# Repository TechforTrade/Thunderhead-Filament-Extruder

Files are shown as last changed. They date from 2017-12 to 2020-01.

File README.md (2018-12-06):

# Thunderhead Filament Extruder

The Thunderhead filament extruder is a  small scale extruder designed by Techfortrade that can be used for recycling PET plastic bottle flake directly into 3D printing filament. A special emphasis throughout the design has been placed on using affordable and easily attainable materials. This repository serves as a host for the documentation and code used with the machine. We are using GrabCAD Workbench for the hardware development and will place snapshots of the CAD files here on Github with each release. Current (though not necessarily stable) files can be accessed on our [GrabCAD partner space](https://workbench.grabcad.com/workbench/projects/gcvN9Xsi01SW-lFGhJRj_-4vqndCMFAaoUt_-UQBdidnVn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).

#### The Thunderhead converts clean and dry PET flake into 3D printing Filament
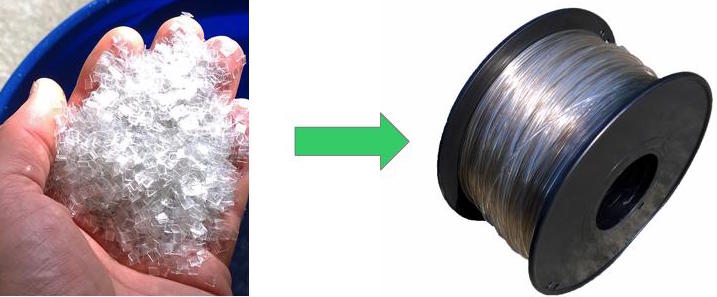
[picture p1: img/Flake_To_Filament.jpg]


# Table of Contents

- [Goals](#goals)
- [PET Plastic](#pet-plastic)
- [Safety and Liability](#safety-and-liability)
- [Building the Thunderhead](#building-the-thunderhead)
- [Software](#software)
- [Operation](#operation)
- [Contributing](#contributing)
- [Maintainers](#maintainers)
- [Acknowledgements](#acknowledgements)
- [License](#license)

## Goals
The Thunderhead is designed with the intent of making it possible to recycle plastic from the post consumer waste stream into 3D printing filament on a small scale with minimal start up capital required. This makes the following possible:
- Low cost 3D printing filament anywhere in the world
- Enable local capture of the value contained in waste plastic
- Access to expensive or hard to find items via 3D printing (eg. [Open Flexure Microscope](https://github.com/rwb27/openflexure_microscope))
- Small scale business opportunities without need for large amounts of capital
- Enable local recycling where it is otherwise not possible

## PET Plastic 
The Thunderhead is designed to extrude Polyethylene Terephthalate (PET or PETE) for the following reasons:

-  Prints  very well on printers such as the Retr3D
-  Easy to find nearly anywhere on the planet
-  Has good physical properties
-  Reasonably safe to work with, especially compared to ABS which often has Brominated Flame Retardants (BFR)

PET is easily identified by the following symbol usually located on the bottom on the bottle:

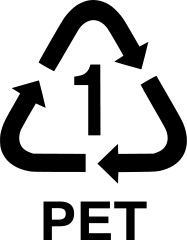
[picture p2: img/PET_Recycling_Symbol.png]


There are some challenges to working with PET plastic. A few these are described below. Follow the links to get more detailed information on these and other challenges:

* **Crystalization** - PET crystalizes when cooled slowly. To avoid making filament that is brittle like glass, a water bath is used.
* **Low Viscosity** - When PET melts it has a low viscosity and a low melt strength which makes it difficult to pull into a filament with an even diameter. The Thunderhead uses a cooling tube to help increase the viscosity and melt strength before the plastic leaves the extruder. The water bath also helps to 
* **Hygroscopicity** - PET pulls water out of the air and holds on to it. This water can cause problems during extrusion and printing such as air bubbles, foaming and degredation of the plastic.
* **Hydrolysis** - The polymer chains in PET can break down in the presence of water at elevated temperatures. When this happens, the viscosity of the melt is reduced, making it difficult to extrude. To Avoid this problem, the plastic flakes must be thoroughly dried just before extrusion. 

## Safety and Liability

You are responsible for your own safety. This machine is under development. Please see the text in the license regarding **Disclaimer of Warranties and Limitation of Liability**.

## Building the Thunderhead

Please refer to our [wiki](https://github.com/TechforTrade/Thunderhead-Filament-Extruder/wiki) for detailed information on building the Thunderhead. 

#### Major Tools Needed ####

Note that you don't necessarily have to own all of these tools. A local shop could do some of the work for you. Especially the lathe and milling work. See the Wiki for a more exhaustive list.

* Drill Press
* Metal Lathe - Threading the barrel and making the shaft for the gear box
* Welding (stick, oxy-acetalene, etc.) - For welding frames together
* 3D printer - Many of the complex parts in the machine are 3D printed
* Milling Machine (optional) - For milling flats into a few parts. Could be done with grinder and hand files though more time consuming.
* Horizontal band saw (optional) - For cutting stock metal to size. A hacksaw and vice will work, but will be slower.

#### Major Components of the Thunderhead

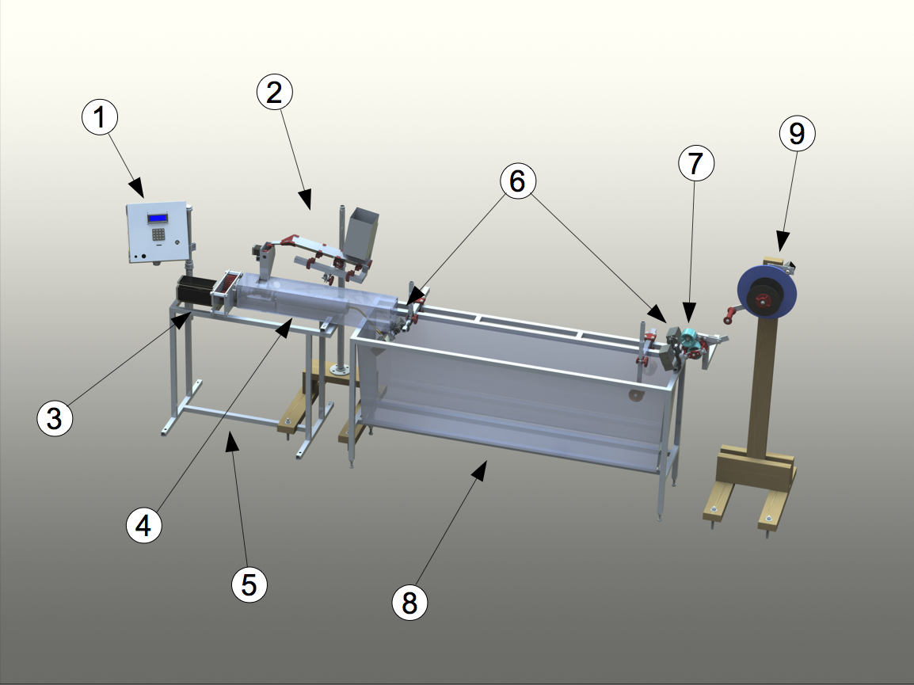
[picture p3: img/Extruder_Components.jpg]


1. **Control Box** - Contains the power supply, Arduino, and other circuitry needed to operate the extruder. Note: The starve feeder, diameter sensors and spooler have their own control circuitry and communicate with the master Arduino via IIC.
2. **Starve Feeder**- Used to add flakes to the extruder at a constent rate. Subcomponents are:
   1. Hopper - Holdes flake ready to be extruded
   2. Vibratory Conveyer - Moves flake to the balance and keeps flake from bridging, and rat holing.
   3. Balance - Weighs out small portions of flake and then delivers them to the extruder at a constant rate. Feedback from the balance controls the vibratory conveyer.
3. **Auger Motor and Gear Box** - A large NEMA 42 stepper motor and 3:1 gear box with 3D printed gears. The stepper alows for speed control and the gearbox increases the torque on the auger.
4. **Extruder Body** - The extruder body has many components. The main components are:
   1. Feed Throat - Location where the plastic enters the barrel. Made with internal grooves to improve the feeding of the plastic into the barrel.
   2. Auger - A 1/2 in. diameter, 18 in. long wood auger used to convey the plastic through the barrel. NOTE: This is not designed for plastics extrusion and performs significantly worse than a plastic extrusion screw would. It is much less expensive though.
   3. Barrel - 1/2in I.D. DOM metal pipe through which the auger pushes the plastic. It has two heating zones that are heated by 104 watt 1/2 in. fiberglass insulated heating tape.
   4. Breaker plate - A small disk of metal with a number of holes drilled into it at the downstream end of the barrel. It acts to reduce the twist in the plastic that is caused by the screw, reducing what is called "screw beat" and improving the uniformity of the diameter. 
   5. Cooling tube - A brass tube at the end of the barrel that reduces the temperature of the plastic melt in order to increase its viscosity. The bend in the tube helps to aim the filament at the guide roller at the end of the water bath and improve roundness of the filament. It has two heating zones.
   6. Nozzle - determines diameter of melt as it leaves the extruder. Equiped with its own heating zone so that surface quality of the filament can be improved.
5. **Extruder Stand** - Supports the extruder and has a sheet metal enclosure to collect fumes given off by the extruder.
6. **Diameter Sensors** - Non contact laser diameter sensors with their own control electronics. The first is used to determine the diameter of the melt as it leaves the extruder and control the speed of the outfeed rollers in order to maintain a constant diameter. The second is used to monitor the final diameter and ensure that the set point of the first diameter sensor is correct.
7. **Outfeed Rollers** - Used to pull the filament through the water bath. Their speed determines the diameter of the filament. The rollers are controlled by the primary diameter sensor.
8. **Water Bath** - Used to cool the melt quickly. This is important because otherwise, the PET would neck down to a very small diameter or cool too slowly and crystalize. Crystalized plastic is too brittle to work with a 3D printer.
9. **Spooler** - Winds the filament up onto a spool. The spooler is still being worked on, early designs fought with the outfeed rollers and caused uneven filament diameters.

## Software

Please refer to our [wiki](https://github.com/TechforTrade/Thunderhead-Filament-Extruder/wiki) for detailed information on the use of the various bits of code kept in this repository.

Five firmware installations must be completed to get the Thunderhead up and running. These are:

- **Thunderware.ino** - for the Arduino mega 2560 that controls the machine (located in the controller box)
- **StarveFeeder.ino** - Upload to the Arduino Nano that controls the starve feeder.
- **Diameter_Sensor.ino (x2)** - Install on <u>both</u> the primary and QC diameter sensor Arduino Nanos.
- **Spooler.ino** - Upload to the Arduino Nano that controls the spooler.

Additionally, there is code written in Processing called **Extruder_Data_visualizer.pde** that produces real time graphs of the the output of the diameter sensors as well as the outfeed roller RPM. This can be useful for tuning the PID in the primary diameter sensor that controls the filament diameter.

## Operation

Detailed operation instructions with tips and trouble shooting are located in our [wiki](https://github.com/TechforTrade/Thunderhead-Filament-Extruder/wiki). The following summarizes basic operation. Video of this process can be found here.

#### Preparation

Before extruding, the clean PET flake must be dried. This must happen just before extruding because the PET will absorb water out of the air at room temperature. Dry the PET in a bench top oven (toaster oven) at a temperature between 150 and 170 °C for four hours. Do this in a well ventilated area. It is recomended to capture and vent the fumes with a fume hood and duct. Do not exceed 175 °C as the plastic will begin to degrade. Keep the flake in the oven until the extruder is ready to begin extruding so that the flake is exposed to room temperature air for as little time as possible.

#### Extruding

Steps

1. Power up the extruder. 
2. Select the menu option "Select Profile". For this and all following steps:
   1.  'A' is used to scroll up.
   2.  'B' is used to scoll down.
   3.  'C' is used to select.
3. Select the profile you want.
4. Select "Extrude".
   1. The extruder will enter the Preheat state, and warm the heating zones to the initial set temps.
5. When the initial set temps have been reached, the extruder will automatically enter the Soak state and soak for the number of minutes specified in the profile.
6. While the extruder is in the Soak state do the following:
   1. Remove the plastic from the oven and add it to the hopper.
   2. Home the balance by rotating the balance counter clockwise as far as it will go and then selecting "Home Balance" from the menu.
   3. Select "Feed Plastic" to turn the vibratory conveyer on.
   4. Turn the vibratory conveyor off when the flake has moved to then end of the conveyor and is about to begin filling the bucket by selecting "Feed Plastic" again.
7. At the end of the Soak state (default time is 8 minutes) the extruder will automatically enter the Extrude state.
8. Turn on the starve feeder by selecting "Starve Feeder".
9. When plastic begins to flow out of the nozzle, use the start up tool to guide the filament under the guide roller in the water bath and then place the filament between the outfeed rollers.
10. Reduce the temperatures to the extruding temperatures (the cooling tube and nozzle temps are lowered) by selecting  "Set Extrude Temps" from the menu.
11. Increase the diameter of the filament to the desired diameter by reducing the outfeed RPM. Do this by selecting "Outfeed RPM" and entering the desired rpm (typically around 18).
12. Clip off the initial section of filament that is not of the correct diameter.
13. Load the filament into the spooler and turn it on. 
14. If desired, automatic control of the outfeed roller rpm can be engaged by selecting "OF Mode". It will change from "man" to "auto". The rpm of the outfeed rollers will now be automatically adjusted to maintain the "Dia Setpoint".

#### Stopping the Extruder

At any point during the extrusion (including preheat and soak) the extruder can be stopped by pressing 'D'. You will be asked to confirm by pressing 'A' or cancel by pressing 'B'. The machine can also simply be powered off.

## Contributing

We'd love your help! You can contribute in many ways. Here are a few:

* Technical support on designs, code etc.
* Help improve the wiki and other documentation.
* Testing. Different Extrusion parameters, code, etc.
* Connect us with other interested individuals and groups.
* Donate! [Techfortrade](http://www.techfortrade.org/) is a non profit organization working to create business opportunities in low resource settings.
<a href="https://www.globalgiving.org/projects/digital-blacksmiths-3d-printing-from-trash/">Donate Now</a>

## On Going Work

All the of the most up to date CAD files can be found [here on our GrabCAD Workbench](https://workbench.grabcad.com/workbench/projects/gcvN9Xsi01SW-lFGhJRj_-4vqndCMFAaoUt_-UQBdidnVn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). The following are a few ideas that we are hoping to pursue:

### Planned Improvements and Experiments ###

#### Feedback Control####

The non-contact diameter sensors are now working so we can get real time information on diameter. The code for using feedback control to maintain constant diameter is also mostly in place. What needs to be done now is to find the correct  placement of the sensor and tune the PID. 

#### Drying hopper ####

Currently the plastic is dried and then put into the hopper where it sits and
absorbs moisture. With a drying hopper, the plastic would be continuously dried
and would have no chance to absorb moisture before entering the machine. This
may help improve the melt viscosity and consistency by reducing the amount of polymer
hydrolysis.

#### New Filament Support/Guiding Strategy ####
The shape and diameter of the filament is essentially set when the hot plastic
enters the water bath. Unwanted movement of the filament down stream from this
point can greatly impact the shape of the filament. New strategies for guiding
the filament in a controlled manner need to be explored. 

#### Nozzle Geometry and Drawdown ####
It may be fruitful to explore different nozzle geometries and the amount and
rate of drawdown. What are the optimal conditions for consistent filament?

#### Test Different Sources of PET ####
Not all PET resins are the same. By testing resins from various bottle sources
and even virgin pellets, it may be possible to determine whether or not some
sources have more desirable characteristics than others.

#### Melt Filter ####
A screen should be added just up stream of the breaker plate. This screen will
catch debris and improve the quality of the filament. A down side is that a melt filter may reduce, perhaps greatly, the output of the machine.

#### Explore potential additives

Desiccating agents such as CaO (quicklime) or even Portland cement might
possibly be added to scavenge water remaining in the melt, which would help
improve viscosity. Nucleating agents such as sodium benzoate and talc might be
used to encourage crystal growth, growing more numerous and smaller crystals
which may help to reduce the brittleness of crystalline polymer. Could this be a route to producing printable crystalline PET?

## Maintainers

[Matthew Rogge](https://github.com/Maaphoo) and [Michael Uttmark](https://github.com/biosafetylvl5) are currently the maintainers of this
repository.

## Acknowledgements

The following people and organizations provided valuable help and guidance over
the course of the project:

**Matt Clark** who provided hundreds of free man hours to assist with the re-design process.

**Frank Schoofs** who volunteered his material science expertise to assist with thermal modeling required to design heating and cooling sections of the extruder.

**Vasileios Grammatikakis** an electronics expert who has assisted with improvements to the Thunderhead electronics.

**Unilever plc.** whose PET specialists have provided insights into working with PET, drying, and testing.

## 

## License


This work is licensed under a <a rel="license" href="http://creativecommons.org/licenses/by-sa/4.0/">Creative Commons Attribution-ShareAlike 4.0 International License</a>.

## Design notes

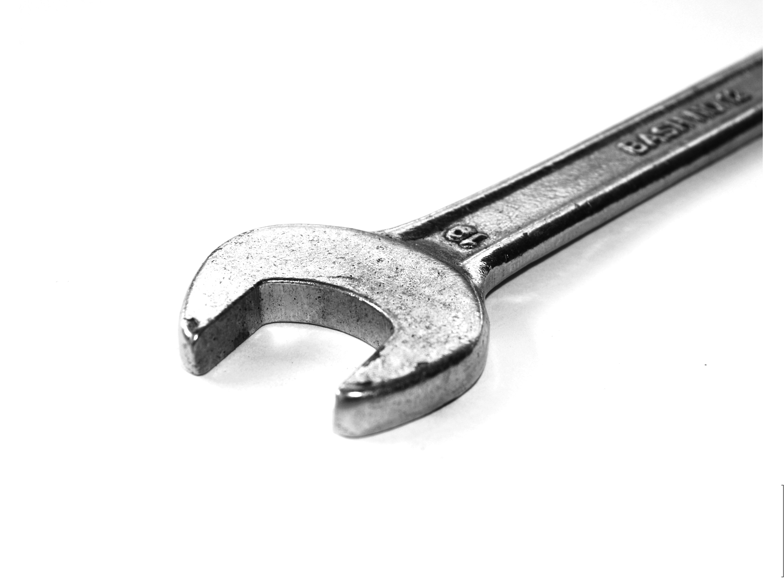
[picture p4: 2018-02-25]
img/Tools/wrench.jpg

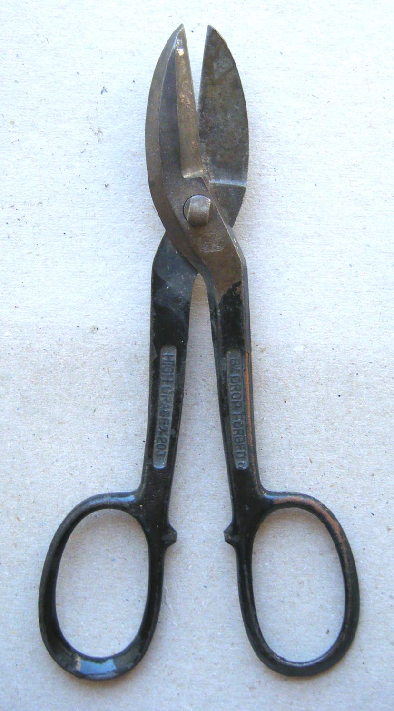
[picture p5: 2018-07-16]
img/Tools/Tin Snips.jpg

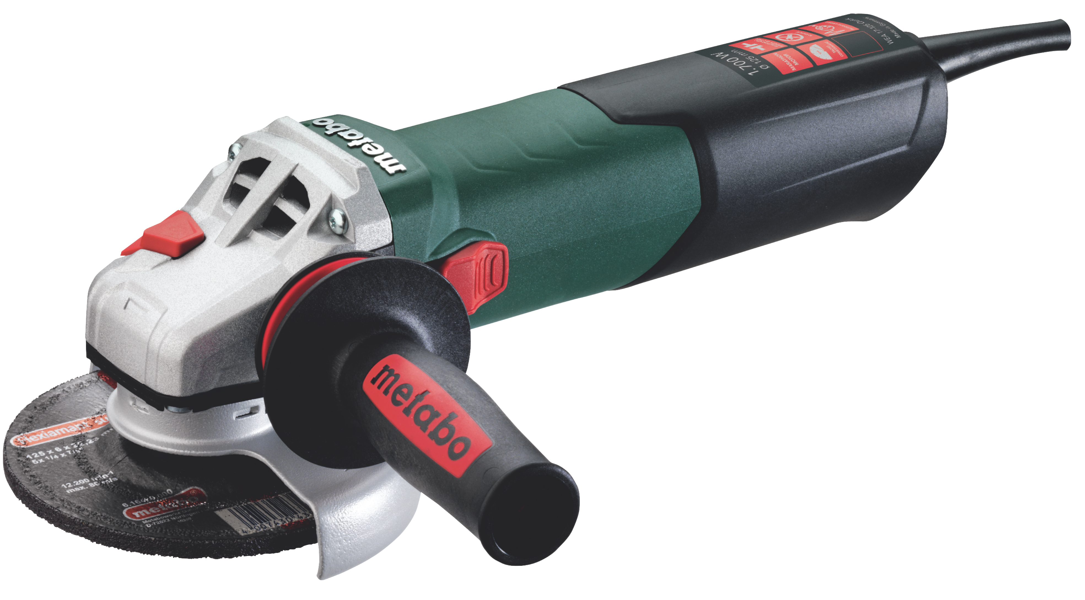
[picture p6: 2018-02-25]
img/Tools/Angle Grinder.jpg

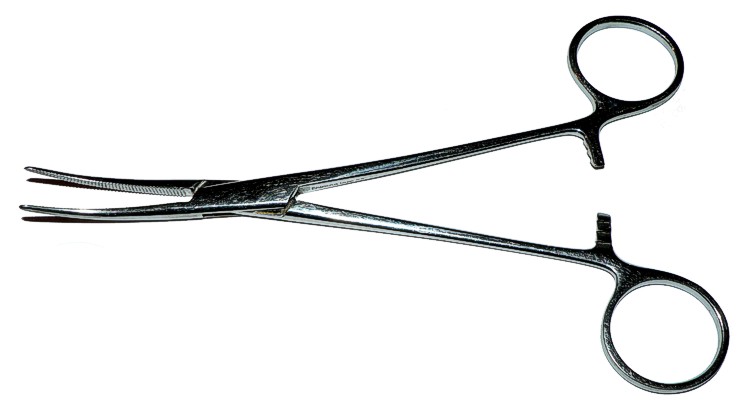
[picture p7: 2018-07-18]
img/Tools/Hemostat.jpg

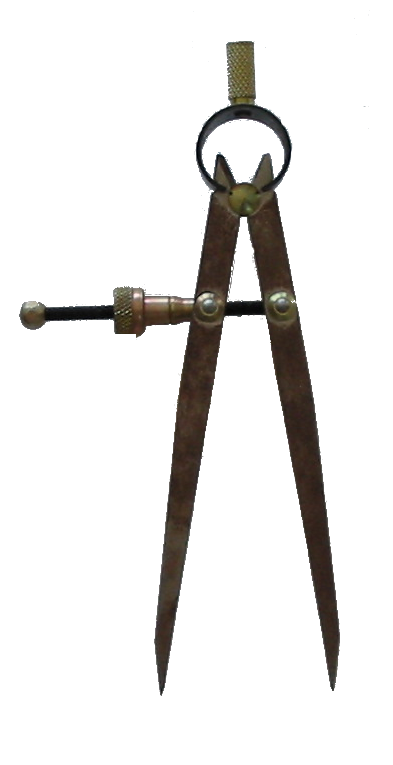
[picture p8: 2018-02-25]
img/Tools/Spring Divider.png

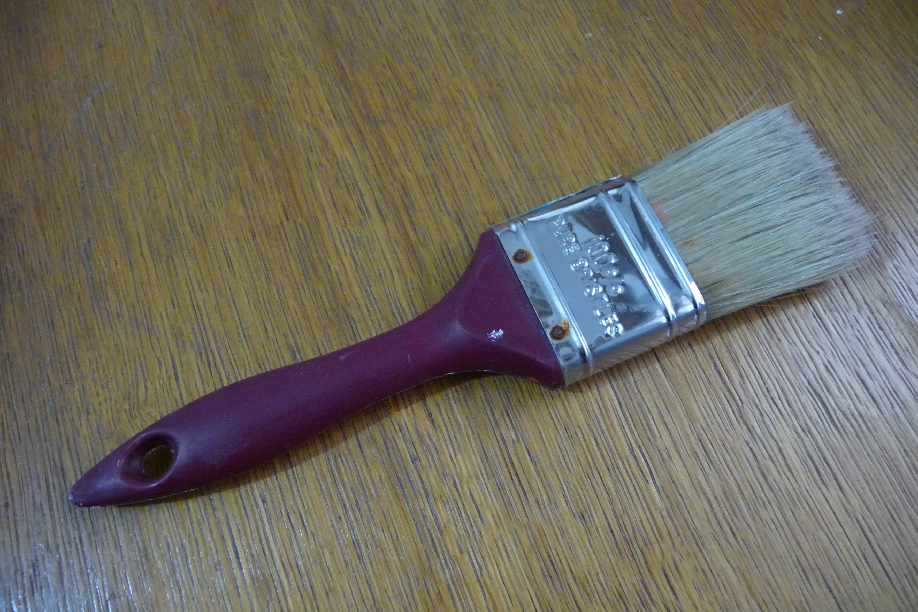
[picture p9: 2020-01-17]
img/Tools/Paint Brush.jpg

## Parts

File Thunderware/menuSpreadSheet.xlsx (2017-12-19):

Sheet: Sheet1
id | Text | parent | child | value | precision | type | action
0 | root | -1 | 1 | NULL | 0 | Menu::TITLE | NULL | {rootStr, -1, 1, NULL, 0, Menu::TITLE, NULL},
1 | selectProfile | 0 | 4 | NULL | 0 | Menu::TITLE | NULL | {selectProfileStr, 0, 4, NULL, 0, Menu::TITLE, NULL},
2 | calibrate | 0 | 35 | NULL | 0 | Menu::TITLE | NULL | {calibrateStr, 0, 35, NULL, 0, Menu::TITLE, NULL},
3 | auxiliary | 0 | 119 | NULL | 0 | Menu::TITLE | NULL | {auxiliaryStr, 0, 119, NULL, 0, Menu::TITLE, NULL},
4 | profile0 | 1 | 15 | &configuration.profileNames[0] | 0 | Menu::TITLE_STRING | &loadProfile0 | {profile0Str, 1, 15, &configuration.profileNames[0], 0, Menu::TITLE_STRING, &loadProfile0},
5 | profile1 | 1 | 15 | &configuration.profileNames[1] | 0 | Menu::TITLE_STRING | &loadProfile1 | {profile1Str, 1, 15, &configuration.profileNames[1], 0, Menu::TITLE_STRING, &loadProfile1},
6 | profile2 | 1 | 15 | &configuration.profileNames[2] | 0 | Menu::TITLE_STRING | &loadProfile2 | {profile2Str, 1, 15, &configuration.profileNames[2], 0, Menu::TITLE_STRING, &loadProfile2},
7 | profile3 | 1 | 15 | &configuration.profileNames[3] | 0 | Menu::TITLE_STRING | &loadProfile3 | {profile3Str, 1, 15, &configuration.profileNames[3], 0, Menu::TITLE_STRING, &loadProfile3},
8 | profile4 | 1 | 15 | &configuration.profileNames[4] | 0 | Menu::TITLE_STRING | &loadProfile4 | {profile4Str, 1, 15, &configuration.profileNames[4], 0, Menu::TITLE_STRING, &loadProfile4},
9 | profile5 | 1 | 15 | &configuration.profileNames[5] | 0 | Menu::TITLE_STRING | &loadProfile5 | {profile5Str, 1, 15, &configuration.profileNames[5], 0, Menu::TITLE_STRING, &loadProfile5},
10 | profile6 | 1 | 15 | &configuration.profileNames[6] | 0 | Menu::TITLE_STRING | &loadProfile6 | {profile6Str, 1, 15, &configuration.profileNames[6], 0, Menu::TITLE_STRING, &loadProfile6},
11 | profile7 | 1 | 15 | &configuration.profileNames[7] | 0 | Menu::TITLE_STRING | &loadProfile7 | {profile7Str, 1, 15, &configuration.profileNames[7], 0, Menu::TITLE_STRING, &loadProfile7},
12 | profile8 | 1 | 15 | &configuration.profileNames[8] | 0 | Menu::TITLE_STRING | &loadProfile8 | {profile8Str, 1, 15, &configuration.profileNames[8], 0, Menu::TITLE_STRING, &loadProfile8},
13 | profile9 | 1 | 15 | &configuration.profileNames[9] | 0 | Menu::TITLE_STRING | &loadProfile9 | {profile9Str, 1, 15, &configuration.profileNames[9], 0, Menu::TITLE_STRING, &loadProfile9},
14 | defaultProfile | 1 | 15 | NULL | 0 | Menu::TITLE | &loadDefaultProfile | {defaultProfileStr, 1, 15, NULL, 0, Menu::TITLE, &loadDefaultProfile},
15 | extrude | 4 | -1 | NULL | 0 | Menu::TITLE | &actionExtrude | {extrudeStr, 4, -1, NULL, 0, Menu::TITLE, &actionExtrude},
16 | saveProfile | 4 | -1 | NULL | 0 | Menu::TITLE | &saveCurrentProfile | {saveProfileStr, 4, -1, NULL, 0, Menu::TITLE, &saveCurrentProfile},
17 | profileName | 4 | -1 | &configuration.profile.name | 0 | Menu::STRING | NULL | {profileNameStr, 4, -1, &configuration.profile.name, 0, Menu::STRING, NULL},
18 | diaSetpoint | 4 | -1 | &configuration.profile.diaSetpoint | 2 | Menu::DOUBLE | NULL | {diaSetpointStr, 4, -1, &configuration.profile.diaSetpoint, 2, Menu::DOUBLE, NULL},
19 | density | 4 | -1 | &configuration.profile.density | 2 | Menu::DOUBLE | NULL | {densityStr, 4, -1, &configuration.profile.density, 2, Menu::DOUBLE, NULL},
20 | tolerance | 4 | -1 | &configuration.profile.tolerance | 2 | Menu::FLOAT | NULL | {toleranceStr, 4, -1, &configuration.profile.tolerance, 2, Menu::FLOAT, NULL},
21 | gramsPerMin | 4 | -1 | &configuration.profile.gramsPerMin | 2 | Menu::FLOAT | NULL | {gramsPerMinStr, 4, -1, &configuration.profile.gramsPerMin, 2, Menu::FLOAT, NULL},
22 | augerRPM | 4 | -1 | &configuration.profile.augerRPM | 1 | Menu::FLOAT | NULL | {augerRPMStr, 4, -1, &configuration.profile.augerRPM, 1, Menu::FLOAT, NULL},
23 | outfeedRPM | 4 | -1 | &configuration.profile.outfeedRPM | 1 | Menu::DOUBLE | NULL | {outfeedRPMStr, 4, -1, &configuration.profile.outfeedRPM, 1, Menu::DOUBLE, NULL},
24 | soakTime | 4 | -1 | &configuration.profile.soakTime | 0 | Menu::DOUBLE | NULL | {soakTimeStr, 4, -1, &configuration.profile.soakTime, 0, Menu::DOUBLE, NULL},
25 | zone1InitialSetTemp | 4 | -1 | &configuration.profile.zone1InitialSetTemp | 0 | Menu::DOUBLE | NULL | {zone1InitialSetTempStr, 4, -1, &configuration.profile.zone1InitialSetTemp, 0, Menu::DOUBLE, NULL},
26 | zone2InitialSetTemp | 4 | -1 | &configuration.profile.zone2InitialSetTemp | 0 | Menu::DOUBLE | NULL | {zone2InitialSetTempStr, 4, -1, &configuration.profile.zone2InitialSetTemp, 0, Menu::DOUBLE, NULL},
27 | zone3InitialSetTemp | 4 | -1 | &configuration.profile.zone3InitialSetTemp | 0 | Menu::DOUBLE | NULL | {zone3InitialSetTempStr, 4, -1, &configuration.profile.zone3InitialSetTemp, 0, Menu::DOUBLE, NULL},
28 | zone4InitialSetTemp | 4 | -1 | &configuration.profile.zone4InitialSetTemp | 0 | Menu::DOUBLE | NULL | {zone4InitialSetTempStr, 4, -1, &configuration.profile.zone4InitialSetTemp, 0, Menu::DOUBLE, NULL},
29 | zone5InitialSetTemp | 4 | -1 | &configuration.profile.zone5InitialSetTemp | 0 | Menu::DOUBLE | NULL | {zone5InitialSetTempStr, 4, -1, &configuration.profile.zone5InitialSetTemp, 0, Menu::DOUBLE, NULL},
30 | zone1SetTemp | 4 | -1 | &configuration.profile.zone1SetTemp | 0 | Menu::DOUBLE | NULL | {zone1SetTempStr, 4, -1, &configuration.profile.zone1SetTemp, 0, Menu::DOUBLE, NULL},
31 | zone2SetTemp | 4 | -1 | &configuration.profile.zone2SetTemp | 0 | Menu::DOUBLE | NULL | {zone2SetTempStr, 4, -1, &configuration.profile.zone2SetTemp, 0, Menu::DOUBLE, NULL},
32 | zone3SetTemp | 4 | -1 | &configuration.profile.zone3SetTemp | 0 | Menu::DOUBLE | NULL | {zone3SetTempStr, 4, -1, &configuration.profile.zone3SetTemp, 0, Menu::DOUBLE, NULL},
33 | zone4SetTemp | 4 | -1 | &configuration.profile.zone4SetTemp | 0 | Menu::DOUBLE | NULL | {zone4SetTempStr, 4, -1, &configuration.profile.zone4SetTemp, 0, Menu::DOUBLE, NULL},
34 | zone5SetTemp | 4 | -1 | &configuration.profile.zone5SetTemp | 0 | Menu::DOUBLE | NULL | {zone5SetTempStr, 4, -1, &configuration.profile.zone5SetTemp, 0, Menu::DOUBLE, NULL},
35 | saveConfig | 2 | -1 | NULL | 0 | Menu::ACTION | &saveConfig | {saveConfigStr, 2, -1, NULL, 0, Menu::ACTION, &saveConfig},
36 | starveFeederConfig | 2 | 41 | NULL | 0 | Menu::TITLE | NULL | {starveFeederConfigStr, 2, 41, NULL, 0, Menu::TITLE, NULL},
37 | augerConfig | 2 | 65 | NULL | 0 | Menu::TITLE | NULL | {augerConfigStr, 2, 65, NULL, 0, Menu::TITLE, NULL},
38 | heaterConfig | 2 | 71 | NULL | 0 | Menu::TITLE | NULL | {heaterConfigStr, 2, 71, NULL, 0, Menu::TITLE, NULL},
39 | outfeedConfig | 2 | 109 | NULL | 0 | Menu::TITLE | NULL | {outfeedConfigStr, 2, 109, NULL, 0, Menu::TITLE, NULL},
40 | spoolerConfig | 2 | 110 | NULL | 0 | Menu::TITLE | NULL | {spoolerConfigStr, 2, 110, NULL, 0, Menu::TITLE, NULL},
41 | homeStarveFeeder | 36 | -1 | NULL | 0 | Menu::ACTION | &homeStarveFeeder | {homeStarveFeederStr, 36, -1, NULL, 0, Menu::ACTION, &homeStarveFeeder},
42 | dump | 36 | -1 | NULL | 0 | Menu::ACTION | &dump | {dumpStr, 36, -1, NULL, 0, Menu::ACTION, &dump},
43 | feed | 36 | -1 | &feedMode | 0 | Menu::STRING_LOCKED | &feed | {feedStr, 36, -1, &feedMode, 0, Menu::STRING_LOCKED, &feed},
44 | sendCycles | 36 | -1 | NULL | 0 | Menu::ACTION | &sendCyclesToStarveFeeder | {sendCyclesStr, 36, -1, NULL, 0, Menu::ACTION, &sendCyclesToStarveFeeder},
45 | cyclesToSendToStarveFeeder | 36 | -1 | &cyclesToSendToStarveFeeder | 0 | Menu::INT | NULL | {cyclesToSendToStarveFeederStr, 36, -1, &cyclesToSendToStarveFeeder, 0, Menu::INT, NULL},
46 | sendTime | 36 | -1 | NULL | 0 | Menu::ACTION | &sendTimeToStarveFeeder | {sendTimeStr, 36, -1, NULL, 0, Menu::ACTION, &sendTimeToStarveFeeder},
47 | timeToSendToStarveFeeder | 36 | -1 | &timeToSendToStarveFeeder | 0 | Menu::INT | NULL | {timeToSendToStarveFeederStr, 36, -1, &timeToSendToStarveFeeder, 0, Menu::INT, NULL},
48 | gramsPerMin | 36 | -1 | &configuration.profile.gramsPerMin | 2 | Menu::FLOAT | NULL | {gramsPerMinStr, 36, -1, &configuration.profile.gramsPerMin, 2, Menu::FLOAT, NULL},
49 | stop | 36 | -1 | NULL | 0 | Menu::ACTION | &stopStarveFeeder | {stopStr, 36, -1, NULL, 0, Menu::ACTION, &stopStarveFeeder},
50 | starveFeederSlaveAddress | 36 | -1 | &configuration.physical.starveFeederSlaveAddress | 0 | Menu::INT | NULL | {starveFeederSlaveAddressStr, 36, -1, &configuration.physical.starveFeederSlaveAddress, 0, Menu::INT, NULL},
51 | starveFeederLumpMass | 36 | -1 | &configuration.physical.starveFeederLumpMass | 2 | Menu::FLOAT | NULL | {starveFeederLumpMassStr, 36, -1, &configuration.physical.starveFeederLumpMass, 2, Menu::FLOAT, NULL},
52 | starveFeederHomePosition | 36 | -1 | &configuration.physical.starveFeederHomePosition | 0 | Menu::INT | NULL | {starveFeederHomePositionStr, 36, -1, &configuration.physical.starveFeederHomePosition, 0, Menu::INT, NULL},
53 | starveFeederDumpPosition | 36 | -1 | &configuration.physical.starveFeederDumpPosition | 0 | Menu::INT | NULL | {starveFeederDumpPositionStr, 36, -1, &configuration.physical.starveFeederDumpPosition, 0, Menu::INT, NULL},
54 | starveFeederStepDelay | 36 | -1 | &configuration.physical.starveFeederStepDelay | 0 | Menu::INT | NULL | {starveFeederStepDelayStr, 36, -1, &configuration.physical.starveFeederStepDelay, 0, Menu::INT, NULL},
55 | starveFeederHomingStepDelay | 36 | -1 | &configuration.physical.starveFeederHomingStepDelay | 0 | Menu::INT | NULL | {starveFeederHomingStepDelayStr, 36, -1, &configuration.physical.starveFeederHomingStepDelay, 0, Menu::INT, NULL},
56 | starveFeederOverRotation | 36 | -1 | &configuration.physical.starveFeederOverRotation | 0 | Menu::INT | NULL | {starveFeederOverRotationStr, 36, -1, &configuration.physical.starveFeederOverRotation, 0, Menu::INT, NULL},
57 | starveFeederDirection | 36 | -1 | &configuration.physical.starveFeederDirection | 0 | Menu::BOOLEAN | NULL | {starveFeederDirectionStr, 36, -1, &configuration.physical.starveFeederDirection, 0, Menu::BOOLEAN, NULL},
58 | starveFeederVibDutyCycle | 36 | -1 | &configuration.physical.starveFeederVibDutyCycle | 0 | Menu::INT | NULL | {starveFeederVibDutyCycleStr, 36, -1, &configuration.physical.starveFeederVibDutyCycle, 0, Menu::INT, NULL},
59 | starveFeederStartupDutyCycle | 36 | -1 | &configuration.physical.starveFeederStartupDutyCycle | 0 | Menu::INT | NULL | {starveFeederStartupDutyCycleStr, 36, -1, &configuration.physical.starveFeederStartupDutyCycle, 0, Menu::INT, NULL},
60 | starveFeederMaxDutyCycle | 36 | -1 | &configuration.physical.starveFeederMaxDutyCycle | 0 | Menu::INT | NULL | {starveFeederMaxDutyCycleStr, 36, -1, &configuration.physical.starveFeederMaxDutyCycle, 0, Menu::INT, NULL},
61 | starveFeederMinFillTime | 36 | -1 | &configuration.physical.starveFeederMinFillTime | 0 | Menu::INT | NULL | {starveFeederMinFillTimeStr, 36, -1, &configuration.physical.starveFeederMinFillTime, 0, Menu::INT, NULL},
62 | starveFeederMaxFillTime | 36 | -1 | &configuration.physical.starveFeederMaxFillTime | 0 | Menu::INT | NULL | {starveFeederMaxFillTimeStr, 36, -1, &configuration.physical.starveFeederMaxFillTime, 0, Menu::INT, NULL},
63 | starveFeederStartupTime | 36 | -1 | &configuration.physical.starveFeederStartupTime | 0 | Menu::INT | NULL | {starveFeederStartupTimeStr, 36, -1, &configuration.physical.starveFeederStartupTime, 0, Menu::INT, NULL},
64 | starveFeederDebounceTime | 36 | -1 | &configuration.physical.starveFeederDebounceTime | 0 | Menu::INT | NULL | {starveFeederDebounceTimeStr, 36, -1, &configuration.physical.starveFeederDebounceTime, 0, Menu::INT, NULL},
65 | testAuger | 37 | -1 | NULL | 0 | Menu::ACTION | &testAuger | {testAugerStr, 37, -1, NULL, 0, Menu::ACTION, &testAuger},
66 | augerPinSet | 37 | -1 | &configuration.physical.augerPinSet | 0 | Menu::INT | NULL | {augerPinSetStr, 37, -1, &configuration.physical.augerPinSet, 0, Menu::INT, NULL},
67 | augerStepMode | 37 | -1 | &configuration.physical.augerStepMode | 0 | Menu::INT | NULL | {augerStepModeStr, 37, -1, &configuration.physical.augerStepMode, 0, Menu::INT, NULL},
68 | augerDirection | 37 | -1 | &configuration.physical.augerDirection | 0 | Menu::BOOLEAN | NULL | {augerDirectionStr, 37, -1, &configuration.physical.augerDirection, 0, Menu::BOOLEAN, NULL},
69 | augerEnable | 37 | -1 | &configuration.physical.augerEnable | 0 | Menu::BOOLEAN | NULL | {augerEnableStr, 37, -1, &configuration.physical.augerEnable, 0, Menu::BOOLEAN, NULL},
70 | augerGearRatio | 37 | -1 | &configuration.physical.augerGearRatio | 2 | Menu::FLOAT | NULL | {augerGearRatioStr, 37, -1, &configuration.physical.augerGearRatio, 2, Menu::FLOAT, NULL},
71 | heaterState | 38 | -1 | &heaterState | 0 | Menu::STRING_LOCKED | &toggleHeaterState | {heaterStateStr, 38, -1, &heaterState, 0, Menu::STRING_LOCKED, &toggleHeaterState},
72 | zone1Temp | 38 | -1 | &zone1Temp | 1 | Menu::DOUBLE_LOCKED | NULL | {zone1TempStr, 38, -1, &zone1Temp, 1, Menu::DOUBLE_LOCKED, NULL},
73 | zone2Temp | 38 | -1 | &zone2Temp | 1 | Menu::DOUBLE_LOCKED | NULL | {zone2TempStr, 38, -1, &zone2Temp, 1, Menu::DOUBLE_LOCKED, NULL},
74 | zone3Temp | 38 | -1 | &zone3Temp | 1 | Menu::DOUBLE_LOCKED | NULL | {zone3TempStr, 38, -1, &zone3Temp, 1, Menu::DOUBLE_LOCKED, NULL},
75 | zone4Temp | 38 | -1 | &zone4Temp | 1 | Menu::DOUBLE_LOCKED | NULL | {zone4TempStr, 38, -1, &zone4Temp, 1, Menu::DOUBLE_LOCKED, NULL},
76 | zone5Temp | 38 | -1 | &zone5Temp | 1 | Menu::DOUBLE_LOCKED | NULL | {zone5TempStr, 38, -1, &zone5Temp, 1, Menu::DOUBLE_LOCKED, NULL},
77 | zone1SetTemp | 38 | -1 | &configuration.physical.zone1.setTemp | 0 | Menu::DOUBLE | NULL | {zone1SetTempStr, 38, -1, &configuration.physical.zone1.setTemp, 0, Menu::DOUBLE, NULL},
78 | zone2SetTemp | 38 | -1 | &configuration.physical.zone2.setTemp | 0 | Menu::DOUBLE | NULL | {zone2SetTempStr, 38, -1, &configuration.physical.zone2.setTemp, 0, Menu::DOUBLE, NULL},
79 | zone3SetTemp | 38 | -1 | &configuration.physical.zone3.setTemp | 0 | Menu::DOUBLE | NULL | {zone3SetTempStr, 38, -1, &configuration.physical.zone3.setTemp, 0, Menu::DOUBLE, NULL},
80 | zone4SetTemp | 38 | -1 | &configuration.physical.zone4.setTemp | 0 | Menu::DOUBLE | NULL | {zone4SetTempStr, 38, -1, &configuration.physical.zone4.setTemp, 0, Menu::DOUBLE, NULL},
81 | zone5SetTemp | 38 | -1 | &configuration.physical.zone5.setTemp | 0 | Menu::DOUBLE | NULL | {zone5SetTempStr, 38, -1, &configuration.physical.zone5.setTemp, 0, Menu::DOUBLE, NULL},
82 | zone1TimeBase | 38 | -1 | &configuration.physical.zone1.timeBase | 0 | Menu::INT | NULL | {zone1TimeBaseStr, 38, -1, &configuration.physical.zone1.timeBase, 0, Menu::INT, NULL},
83 | zone1MaxDutyCycle | 38 | -1 | &configuration.physical.zone1.maxDutyCycle | 0 | Menu::DOUBLE | NULL | {zone1MaxDutyCycleStr, 38, -1, &configuration.physical.zone1.maxDutyCycle, 0, Menu::DOUBLE, NULL},
84 | zone1MinDutyCycle | 38 | -1 | &configuration.physical.zone1.minDutyCycle | 0 | Menu::DOUBLE | NULL | {zone1MinDutyCycleStr, 38, -1, &configuration.physical.zone1.minDutyCycle, 0, Menu::DOUBLE, NULL},
85 | zone1Kp | 38 | -1 | &configuration.physical.zone1.Kp | 2 | Menu::DOUBLE | NULL | {zone1KpStr, 38, -1, &configuration.physical.zone1.Kp, 2, Menu::DOUBLE, NULL},
86 | zone1Ki | 38 | -1 | &configuration.physical.zone1.Ki | 2 | Menu::DOUBLE | NULL | {zone1KiStr, 38, -1, &configuration.physical.zone1.Ki, 2, Menu::DOUBLE, NULL},
87 | zone1Kd | 38 | -1 | &configuration.physical.zone1.Kd | 2 | Menu::DOUBLE | NULL | {zone1KdStr, 38, -1, &configuration.physical.zone1.Kd, 2, Menu::DOUBLE, NULL},
88 | zone2TimeBase | 38 | -1 | &configuration.physical.zone2.timeBase | 0 | Menu::INT | NULL | {zone2TimeBaseStr, 38, -1, &configuration.physical.zone2.timeBase, 0, Menu::INT, NULL},
89 | zone2MaxDutyCycle | 38 | -1 | &configuration.physical.zone2.maxDutyCycle | 0 | Menu::DOUBLE | NULL | {zone2MaxDutyCycleStr, 38, -1, &configuration.physical.zone2.maxDutyCycle, 0, Menu::DOUBLE, NULL},
90 | zone2MinDutyCycle | 38 | -1 | &configuration.physical.zone2.minDutyCycle | 0 | Menu::DOUBLE | NULL | {zone2MinDutyCycleStr, 38, -1, &configuration.physical.zone2.minDutyCycle, 0, Menu::DOUBLE, NULL},
91 | zone2Kp | 38 | -1 | &configuration.physical.zone2.Kp | 2 | Menu::DOUBLE | NULL | {zone2KpStr, 38, -1, &configuration.physical.zone2.Kp, 2, Menu::DOUBLE, NULL},
92 | zone2Ki | 38 | -1 | &configuration.physical.zone2.Ki | 2 | Menu::DOUBLE | NULL | {zone2KiStr, 38, -1, &configuration.physical.zone2.Ki, 2, Menu::DOUBLE, NULL},
93 | zone2Kd | 38 | -1 | &configuration.physical.zone2.Kd | 2 | Menu::DOUBLE | NULL | {zone2KdStr, 38, -1, &configuration.physical.zone2.Kd, 2, Menu::DOUBLE, NULL},
94 | zone3MaxDutyCycle | 38 | -1 | &configuration.physical.zone3.maxDutyCycle | 0 | Menu::DOUBLE | NULL | {zone3MaxDutyCycleStr, 38, -1, &configuration.physical.zone3.maxDutyCycle, 0, Menu::DOUBLE, NULL},
95 | zone3MinDutyCycle | 38 | -1 | &configuration.physical.zone3.minDutyCycle | 0 | Menu::DOUBLE | NULL | {zone3MinDutyCycleStr, 38, -1, &configuration.physical.zone3.minDutyCycle, 0, Menu::DOUBLE, NULL},
96 | zone3Kp | 38 | -1 | &configuration.physical.zone3.Kp | 2 | Menu::DOUBLE | NULL | {zone3KpStr, 38, -1, &configuration.physical.zone3.Kp, 2, Menu::DOUBLE, NULL},
97 | zone3Ki | 38 | -1 | &configuration.physical.zone3.Ki | 2 | Menu::DOUBLE | NULL | {zone3KiStr, 38, -1, &configuration.physical.zone3.Ki, 2, Menu::DOUBLE, NULL},
98 | zone3Kd | 38 | -1 | &configuration.physical.zone3.Kd | 2 | Menu::DOUBLE | NULL | {zone3KdStr, 38, -1, &configuration.physical.zone3.Kd, 2, Menu::DOUBLE, NULL},
99 | zone4MaxDutyCycle | 38 | -1 | &configuration.physical.zone4.maxDutyCycle | 0 | Menu::DOUBLE | NULL | {zone4MaxDutyCycleStr, 38, -1, &configuration.physical.zone4.maxDutyCycle, 0, Menu::DOUBLE, NULL},
100 | zone4MinDutyCycle | 38 | -1 | &configuration.physical.zone4.minDutyCycle | 0 | Menu::DOUBLE | NULL | {zone4MinDutyCycleStr, 38, -1, &configuration.physical.zone4.minDutyCycle, 0, Menu::DOUBLE, NULL},
101 | zone4Kp | 38 | -1 | &configuration.physical.zone4.Kp | 2 | Menu::DOUBLE | NULL | {zone4KpStr, 38, -1, &configuration.physical.zone4.Kp, 2, Menu::DOUBLE, NULL},
102 | zone4Ki | 38 | -1 | &configuration.physical.zone4.Ki | 2 | Menu::DOUBLE | NULL | {zone4KiStr, 38, -1, &configuration.physical.zone4.Ki, 2, Menu::DOUBLE, NULL},
103 | zone4Kd | 38 | -1 | &configuration.physical.zone4.Kd | 2 | Menu::DOUBLE | NULL | {zone4KdStr, 38, -1, &configuration.physical.zone4.Kd, 2, Menu::DOUBLE, NULL},
104 | zone5MaxDutyCycle | 38 | -1 | &configuration.physical.zone5.maxDutyCycle | 0 | Menu::DOUBLE | NULL | {zone5MaxDutyCycleStr, 38, -1, &configuration.physical.zone5.maxDutyCycle, 0, Menu::DOUBLE, NULL},
105 | zone5MinDutyCycle | 38 | -1 | &configuration.physical.zone5.minDutyCycle | 0 | Menu::DOUBLE | NULL | {zone5MinDutyCycleStr, 38, -1, &configuration.physical.zone5.minDutyCycle, 0, Menu::DOUBLE, NULL},
106 | zone5Kp | 38 | -1 | &configuration.physical.zone5.Kp | 2 | Menu::DOUBLE | NULL | {zone5KpStr, 38, -1, &configuration.physical.zone5.Kp, 2, Menu::DOUBLE, NULL},
107 | zone5Ki | 38 | -1 | &configuration.physical.zone5.Ki | 2 | Menu::DOUBLE | NULL | {zone5KiStr, 38, -1, &configuration.physical.zone5.Ki, 2, Menu::DOUBLE, NULL},
108 | zone5Kd | 38 | -1 | &configuration.physical.zone5.Kd | 2 | Menu::DOUBLE | NULL | {zone5KdStr, 38, -1, &configuration.physical.zone5.Kd, 2, Menu::DOUBLE, NULL},
109 | RPM | 39 | -1 | &outfeedRPM | 0 | Menu::FLOAT | NULL | {RPMStr, 39, -1, &outfeedRPM, 0, Menu::FLOAT, NULL},
110 | testSpooler | 40 | -1 | NULL | 0 | Menu::ACTION | &testSpooler | {testSpoolerStr, 40, -1, NULL, 0, Menu::ACTION, &testSpooler},
111 | spoolerPinSet | 40 | -1 | &configuration.physical.spoolerPinSet | 0 | Menu::INT | NULL | {spoolerPinSetStr, 40, -1, &configuration.physical.spoolerPinSet, 0, Menu::INT, NULL},
112 | spoolerStepMode | 40 | -1 | &configuration.physical.spoolerStepMode | 0 | Menu::INT | NULL | {spoolerStepModeStr, 40, -1, &configuration.physical.spoolerStepMode, 0, Menu::INT, NULL},
113 | spoolerDirection | 40 | -1 | &configuration.physical.spoolerDirection | 0 | Menu::BOOLEAN | NULL | {spoolerDirectionStr, 40, -1, &configuration.physical.spoolerDirection, 0, Menu::BOOLEAN, NULL},
114 | spoolerEnable | 40 | -1 | &configuration.physical.spoolerEnable | 0 | Menu::BOOLEAN | NULL | {spoolerEnableStr, 40, -1, &configuration.physical.spoolerEnable, 0, Menu::BOOLEAN, NULL},
115 | spoolerDiskRadius | 40 | -1 | &configuration.physical.spoolerDiskRadius | 2 | Menu::FLOAT | NULL | {spoolerDiskRadiusStr, 40, -1, &configuration.physical.spoolerDiskRadius, 2, Menu::FLOAT, NULL},
116 | spoolerCoreRadius | 40 | -1 | &configuration.physical.spoolerCoreRadius | 2 | Menu::FLOAT | NULL | {spoolerCoreRadiusStr, 40, -1, &configuration.physical.spoolerCoreRadius, 2, Menu::FLOAT, NULL},
117 | spoolerTraverseLength | 40 | -1 | &configuration.physical.spoolerTraverseLength | 2 | Menu::FLOAT | NULL | {spoolerTraverseLengthStr, 40, -1, &configuration.physical.spoolerTraverseLength, 2, Menu::FLOAT, NULL},
118 | spoolerMotorRollerRadius | 40 | -1 | &configuration.physical.spoolerMotorRollerRadius | 2 | Menu::FLOAT | NULL | {spoolerMotorRollerRadiusStr, 40, -1, &configuration.physical.spoolerMotorRollerRadius, 2, Menu::FLOAT, NULL},
119 | feed | 3 | -1 | &feedMode | 0 | Menu::STRING_LOCKED | &feed | {feedStr, 3, -1, &feedMode, 0, Menu::STRING_LOCKED, &feed},
120 | measureFilamet | 3 | -1 | NULL | -1 | Menu::ACTION | &measureFilament | {measureFilametStr, 3, -1, NULL, -1, Menu::ACTION, &measureFilament},
121 | resetEEPROM | 3 | -1 | NULL | 0 | Menu::ACTION | &resetEEPROM | {resetEEPROMStr, 3, -1, NULL, 0, Menu::ACTION, &resetEEPROM},
 |  |  |  |  |  |  |  | {Str, , , , , , },
0 | preheatRoot | -1 | 1 | NULL | 0 | Menu::TITLE | &exitPreheat | {preheatRootStr, -1, 1, NULL, 0, Menu::TITLE, &exitPreheat},
1 | zone1Temp | 0 | -1 | &zone1Temp | 1 | Menu::DOUBLE_LOCKED | NULL | {zone1TempStr, 0, -1, &zone1Temp, 1, Menu::DOUBLE_LOCKED, NULL},
2 | zone2Temp | 0 | -1 | &zone2Temp | 1 | Menu::DOUBLE_LOCKED | NULL | {zone2TempStr, 0, -1, &zone2Temp, 1, Menu::DOUBLE_LOCKED, NULL},
3 | zone3Temp | 0 | -1 | &zone3Temp | 1 | Menu::DOUBLE_LOCKED | NULL | {zone3TempStr, 0, -1, &zone3Temp, 1, Menu::DOUBLE_LOCKED, NULL},
4 | zone4Temp | 0 | -1 | &zone4Temp | 1 | Menu::DOUBLE_LOCKED | NULL | {zone4TempStr, 0, -1, &zone4Temp, 1, Menu::DOUBLE_LOCKED, NULL},
5 | zone5Temp | 0 | -1 | &zone5Temp | 1 | Menu::DOUBLE_LOCKED | NULL | {zone5TempStr, 0, -1, &zone5Temp, 1, Menu::DOUBLE_LOCKED, NULL},
6 | zone1InitialSetTemp | 0 | -1 | &configuration.profile.zone1InitialSetTemp | 0 | Menu::DOUBLE | &setZone1Temp | {zone1InitialSetTempStr, 0, -1, &configuration.profile.zone1InitialSetTemp, 0, Menu::DOUBLE, &setZone1Temp},
7 | zone2InitialSetTemp | 0 | -1 | &configuration.profile.zone2InitialSetTemp | 0 | Menu::DOUBLE | &setZone2Temp | {zone2InitialSetTempStr, 0, -1, &configuration.profile.zone2InitialSetTemp, 0, Menu::DOUBLE, &setZone2Temp},
8 | zone3InitialSetTemp | 0 | -1 | &configuration.profile.zone3InitialSetTemp | 0 | Menu::DOUBLE | &setZone3Temp | {zone3InitialSetTempStr, 0, -1, &configuration.profile.zone3InitialSetTemp, 0, Menu::DOUBLE, &setZone3Temp},
9 | zone4InitialSetTemp | 0 | -1 | &configuration.profile.zone4InitialSetTemp | 0 | Menu::DOUBLE | &setZone4Temp | {zone4InitialSetTempStr, 0, -1, &configuration.profile.zone4InitialSetTemp, 0, Menu::DOUBLE, &setZone4Temp},
10 | zone5InitialSetTemp | 0 | -1 | &configuration.profile.zone5InitialSetTemp | 0 | Menu::DOUBLE | &setZone5Temp | {zone5InitialSetTempStr, 0, -1, &configuration.profile.zone5InitialSetTemp, 0, Menu::DOUBLE, &setZone5Temp},
11 | skipPreheat | 0 | -1 | NULL | 0 | Menu::ACTION | &skipPreheat | {skipPreheatStr, 0, -1, NULL, 0, Menu::ACTION, &skipPreheat},
12 | profileName | 0 | -1 | &configuration.profile.name | 0 | Menu::STRING | NULL | {profileNameStr, 0, -1, &configuration.profile.name, 0, Menu::STRING, NULL},
13 | diaSetpoint | 0 | -1 | &configuration.profile.diaSetpoint | 2 | Menu::DOUBLE | NULL | {diaSetpointStr, 0, -1, &configuration.profile.diaSetpoint, 2, Menu::DOUBLE, NULL},
14 | tolerance | 0 | -1 | &configuration.profile.tolerance | 2 | Menu::FLOAT | NULL | {toleranceStr, 0, -1, &configuration.profile.tolerance, 2, Menu::FLOAT, NULL},
15 | gramsPerMin | 0 | -1 | &configuration.profile.gramsPerMin | 2 | Menu::FLOAT | NULL | {gramsPerMinStr, 0, -1, &configuration.profile.gramsPerMin, 2, Menu::FLOAT, NULL},
16 | feed | 0 | -1 | &feedMode | 0 | Menu::STRING_LOCKED | &feed | {feedStr, 0, -1, &feedMode, 0, Menu::STRING_LOCKED, &feed},
17 | augerRPM | 0 | -1 | &configuration.profile.augerRPM | 1 | Menu::FLOAT | NULL | {augerRPMStr, 0, -1, &configuration.profile.augerRPM, 1, Menu::FLOAT, NULL},
18 | outfeedRPM | 0 | -1 | &configuration.profile.outfeedRPM | 1 | Menu::DOUBLE | NULL | {outfeedRPMStr, 0, -1, &configuration.profile.outfeedRPM, 1, Menu::DOUBLE, NULL},
19 | soakTime | 0 | -1 | &configuration.profile.soakTime | 0 | Menu::DOUBLE | NULL | {soakTimeStr, 0, -1, &configuration.profile.soakTime, 0, Menu::DOUBLE, NULL},
0 | soakRoot | -1 | 1 | NULL | 0 | Menu::TITLE | &exitSoak | {soakRootStr, -1, 1, NULL, 0, Menu::TITLE, &exitSoak},
1 | soakTimeRemaining | 0 | -1 | &soakTimeRemaining | 0 | Menu::STRING_LOCKED | NULL | {soakTimeRemainingStr, 0, -1, &soakTimeRemaining, 0, Menu::STRING_LOCKED, NULL},
2 | zone1Temp | 0 | -1 | &zone1Temp | 1 | Menu::DOUBLE_LOCKED | NULL | {zone1TempStr, 0, -1, &zone1Temp, 1, Menu::DOUBLE_LOCKED, NULL},
3 | zone2Temp | 0 | -1 | &zone2Temp | 1 | Menu::DOUBLE_LOCKED | NULL | {zone2TempStr, 0, -1, &zone2Temp, 1, Menu::DOUBLE_LOCKED, NULL},
4 | zone3Temp | 0 | -1 | &zone3Temp | 1 | Menu::DOUBLE_LOCKED | NULL | {zone3TempStr, 0, -1, &zone3Temp, 1, Menu::DOUBLE_LOCKED, NULL},
5 | zone4Temp | 0 | -1 | &zone4Temp | 1 | Menu::DOUBLE_LOCKED | NULL | {zone4TempStr, 0, -1, &zone4Temp, 1, Menu::DOUBLE_LOCKED, NULL},
6 | zone5Temp | 0 | -1 | &zone5Temp | 1 | Menu::DOUBLE_LOCKED | NULL | {zone5TempStr, 0, -1, &zone5Temp, 1, Menu::DOUBLE_LOCKED, NULL},
7 | zone1InitialSetTemp | 0 | -1 | &configuration.profile.zone1InitialSetTemp | 0 | Menu::DOUBLE | &setZone1Temp | {zone1InitialSetTempStr, 0, -1, &configuration.profile.zone1InitialSetTemp, 0, Menu::DOUBLE, &setZone1Temp},
8 | zone2InitialSetTemp | 0 | -1 | &configuration.profile.zone2InitialSetTemp | 0 | Menu::DOUBLE | &setZone2Temp | {zone2InitialSetTempStr, 0, -1, &configuration.profile.zone2InitialSetTemp, 0, Menu::DOUBLE, &setZone2Temp},
9 | zone3InitialSetTemp | 0 | -1 | &configuration.profile.zone3InitialSetTemp | 0 | Menu::DOUBLE | &setZone3Temp | {zone3InitialSetTempStr, 0, -1, &configuration.profile.zone3InitialSetTemp, 0, Menu::DOUBLE, &setZone3Temp},
10 | zone4InitialSetTemp | 0 | -1 | &configuration.profile.zone4InitialSetTemp | 0 | Menu::DOUBLE | &setZone4Temp | {zone4InitialSetTempStr, 0, -1, &configuration.profile.zone4InitialSetTemp, 0, Menu::DOUBLE, &setZone4Temp},
11 | zone5InitialSetTemp | 0 | -1 | &configuration.profile.zone5InitialSetTemp | 0 | Menu::DOUBLE | &setZone5Temp | {zone5InitialSetTempStr, 0, -1, &configuration.profile.zone5InitialSetTemp, 0, Menu::DOUBLE, &setZone5Temp},
12 | increaseSoakTime | 0 | -1 | NULL | 0 | Menu::ACTION | &increaseSoakTime | {increaseSoakTimeStr, 0, -1, NULL, 0, Menu::ACTION, &increaseSoakTime},
13 | decreaseSoakTime | 0 | -1 | NULL | 0 | Menu::ACTION | &decreaseSoakTime | {decreaseSoakTimeStr, 0, -1, NULL, 0, Menu::ACTION, &decreaseSoakTime},
14 | skipSoak | 0 | -1 | NULL | 0 | Menu::ACTION | &skipSoak | {skipSoakStr, 0, -1, NULL, 0, Menu::ACTION, &skipSoak},
15 | homeStarveFeeder | 0 | -1 | NULL | 0 | Menu::ACTION | &homeStarveFeeder | {homeStarveFeederStr, 0, -1, NULL, 0, Menu::ACTION, &homeStarveFeeder},
16 | dump | 0 | -1 | NULL | 0 | Menu::ACTION | &dump | {dumpStr, 0, -1, NULL, 0, Menu::ACTION, &dump},
17 | feed | 0 | -1 | &feedMode | 0 | Menu::STRING_LOCKED | &feed | {feedStr, 0, -1, &feedMode, 0, Menu::STRING_LOCKED, &feed},
18 | profileName | 0 | -1 | &configuration.profile.name | 0 | Menu::STRING | NULL | {profileNameStr, 0, -1, &configuration.profile.name, 0, Menu::STRING, NULL},
19 | diaSetpoint | 0 | -1 | &configuration.profile.diaSetpoint | 2 | Menu::DOUBLE | NULL | {diaSetpointStr, 0, -1, &configuration.profile.diaSetpoint, 2, Menu::DOUBLE, NULL},
20 | tolerance | 0 | -1 | &configuration.profile.tolerance | 2 | Menu::FLOAT | NULL | {toleranceStr, 0, -1, &configuration.profile.tolerance, 2, Menu::FLOAT, NULL},
21 | gramsPerMin | 0 | -1 | &configuration.profile.gramsPerMin | 2 | Menu::FLOAT | NULL | {gramsPerMinStr, 0, -1, &configuration.profile.gramsPerMin, 2, Menu::FLOAT, NULL},
22 | augerRPM | 0 | -1 | &configuration.profile.augerRPM | 1 | Menu::FLOAT | NULL | {augerRPMStr, 0, -1, &configuration.profile.augerRPM, 1, Menu::FLOAT, NULL},
23 | outfeedRPM | 0 | -1 | &configuration.profile.outfeedRPM | 1 | Menu::DOUBLE | NULL | {outfeedRPMStr, 0, -1, &configuration.profile.outfeedRPM, 1, Menu::DOUBLE, NULL},
24 | soakTime | 0 | -1 | &configuration.profile.soakTime | 0 | Menu::DOUBLE | NULL | {soakTimeStr, 0, -1, &configuration.profile.soakTime, 0, Menu::DOUBLE, NULL},
 |  |  |  |  |  |  |  | {Str, , , , , , },
0 | loadFilamentRoot | -1 | 1 | NULL | 0 | Menu::TITLE | &exitLoadFilament | {loadFilamentRootStr, -1, 1, NULL, 0, Menu::TITLE, &exitLoadFilament},
1 | loadFilamentRemainingTime | 0 | -1 | &loadFilamentTimeRemaining | 0 | Menu::STRING_LOCKED | NULL | {loadFilamentRemainingTimeStr, 0, -1, &loadFilamentTimeRemaining, 0, Menu::STRING_LOCKED, NULL},
2 | filamentLoaded | 0 | -1 | NULL | 0 | Menu::ACTION | &filamentLoaded | {filamentLoadedStr, 0, -1, NULL, 0, Menu::ACTION, &filamentLoaded},
3 | loadFilamentAddTime | 0 | -1 | NULL | 0 | Menu::ACTION | &loadFilamentAddTime | {loadFilamentAddTimeStr, 0, -1, NULL, 0, Menu::ACTION, &loadFilamentAddTime},
4 | starveFeederMode | 0 | -1 | &starveFeederMode | 0 | Menu::STRING_LOCKED | &starveFeederChangeMode | {starveFeederModeStr, 0, -1, &starveFeederMode, 0, Menu::STRING_LOCKED, &starveFeederChangeMode},
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

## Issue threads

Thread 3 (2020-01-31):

Printing PET with large noozle

mlapshin, 2020-01-31:
Hello guys, thanks for your awesome work, it's really helpful. I have a PET-related question, if you don't mind.

I'm interested in using PET to print human-scale objects (furniture, containers, sculptures, etc) with large 2mm-5mm nozzles and direct screw extruder. Assuming that flakes are properly dried before extrusion, do you think it's possible to get amorphous PET in result? I doubt that I'll be able to cool down extruded plastic fast enough with a fan, even a heavy one. What do you think of entire idea of using recycled PET to print large objects with thick walls, is PET a good material for that? Do I need to print underwater? :)

I publish my humble experiments [on YouTube](https://www.youtube.com/watch?v=-ZL7SsDM124), but they're in Russian.

Maaphoo, 2020-02-03:
Cool bike. Thanks for the video link.

Printing large scale objects with PET is possible and you are correct that cooling is one of the main issues. Our friends at [Robot 3d Printing](https://www.3d-robotprinting.com/) and [Re:3D](https://re3d.org/) have been printing large objects from PET pellets and pellet/flake mixes. I'm not sure if they have tested the % crystallinity or mechanical properties of their large PET prints, but they are able to get prints that are transparent, suggesting that they haven't completely crystalized. You will likely need some good cooling fans at the nozzle. I've wondered if chilled air would help much. Drooling from larger diameter nozzles is also in issue as PET tends to be fairly low viscosity when melted. One solution to this is to print in spiral vase mode.

Printing large thick walled objects might be fine. It all depends on what the items will be used for and what their mechanical properties are.

One thing that I have read about is adding sodium benzoate or talc to the PET during extrusion. It is supposed to provide nucleation sites for crystal growth. Maybe if smaller more numerous crystals can be formed the mechanical properties can be improved. I am unaware of anyone who has tried it for direct printing or filament. I have always wanted to try.

Printing under water has crossed my mind too! Hats off to anyone who gets that working.

If you decide to work on direct printing with PET, we'd love to know what you find out.

Thanks,

Matt

mlapshin, 2020-02-06:
Hello Matt,

Thanks a lot for you comprehensive answer. The fact that commercial companies are using PET for printing corroborate that it's a right way to go. I've doubted about entire idea, but now I decided to give it a try. I'm finishing bath & puller right now, want to extrude some 1.75 filament and print with it on a desktop printer mostly to satisfy YouTube viewers. Thanks for your suggestion, I think I will do experiment with talc as well, it's pretty easy to buy. Another idea I have is to simulate a 3D printing process manually moving aluminium plate in front of extruder nozzle with a fan blowing on a "printed" model. This might be a cheap way to check if air cooling will work well enough.

I can update this issue with my progress, if you don't mind.

Maaphoo, 2020-02-10:
Would love to hear updates about your progress. It is great to see more people working on printing from PET.

mlapshin, 2020-04-08:
Was able to get almost usable filament, finally:

https://www.youtube.com/watch?v=J1vprT4VFro

Have you guys tried to use V-shaped aluminium extrusion in bath? It works very well for rod stabilising, but deforms filament a little bit, so it comes out not round. I had no luck with pulleys like in your design.

Will try to mix flakes with talc next time. Will let you know. Thanks and take care.

Maaphoo, 2020-04-08:
Nice work! Thanks for the video.

We also had black blobs in our filament at first too. The main issue for us was label glue. We now remove it by wiping the glue with warm cooking oil and then washing with soap and water. Tedious but it works pretty well.

Yes we have moved away from guide rollers and also use an aluminum v in the water bath. The filament is very sensitive to disturbances. A defect catching on anything causes another defect where the plastic is entering the water. A friend recommended a foam coated guide roller at the end of the waterbath do dampen these disturbances.

One way to overcome the issue of imperfect filament is to use a diameter sensor on your 3D printer. We have done so and printed quite successfully. Here's our first print with filament ranging from 1.3 to 1.95 mm in diameter. The sensor measures from 2 different angles so it works ok for filament that isn't perfectly round:
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

kanna19aero, 2020-06-16:
Hi Guys,

you have done a amazing job putting together and great inspiration for the 3d printing community and saving the plastic recycle environment. I would need some help regarding the electrical/electronic bit of it. could you please help me.

Maaphoo, 2020-06-16:
Thanks @kanna19aero

Glad to see you are interested in the machine. Happy to do what we can to help out. Maybe open an issue called "Help with Electronics" or something more specific if you know specifically what your needs are. We can dive into specifics there and it will be available for others who have similar needs.

kanna19aero, 2020-06-16:
Hi TechforTrade/Thunderhead-Filament-Extruder

I ve created the issue under Thunderware electronic bit readiness..

Will this be ok?

Thanks
Kannan

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

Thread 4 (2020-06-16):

Thunderware electronic bit readiness

kanna19aero, 2020-06-16:
Hi Maaphoo,

Thanks for your quick reply.

i request your help to understand the software bit as below. because i have limited knowledge in the coding/software related.

Software
Please refer to our wiki for detailed information on the use of the various bits of code kept in this repository.

Five firmware installations must be completed to get the Thunderhead up and running. These are:

Thunderware.ino - for the Arduino mega 2560 that controls the machine (located in the controller box)
StarveFeeder.ino - Upload to the Arduino Nano that controls the starve feeder.
Diameter_Sensor.ino (x2) - Install on both the primary and QC diameter sensor Arduino Nanos.
Spooler.ino - Upload to the Arduino Nano that controls the spooler.
Additionally, there is code written in Processing called Extruder_Data_visualizer.pde that produces real time graphs of the the output of the diameter sensors as well as the outfeed roller RPM. This can be useful for tuning the PID in the primary diameter sensor that controls the filament diameter.

Thanks,
Kannan

kanna19aero, 2020-06-16:
I have ordered a Arduino kit to understand the functionality and a bit of programming.
Paul McWhorter is a great teacher.

https://www.youtube.com/watch?v=9uHZB7-T_XA&list=PLGs0VKk2DiYw-L-RibttcvK-WBZm8WLEP&index=2

I'm on my 2nd tutorial. Its a great start until I wait for my Arduino kit.

Maaphoo, 2020-06-17:
Great. [Video 1](https://www.youtube.com/watch?v=fJWR7dBuc18&list=PLGs0VKk2DiYw-L-RibttcvK-WBZm8WLEP&index=1) is a great walk through on how to get started. Looks like he gets pretty far "under the hood" in video two. Clear explanations. The video set is a good mix of basic practical skills with in depth explanations.

We are embarking on a general tidy up of our documentation over the next couple of months. When you are going through it, if you have any questions, recommendations or comments, feel free to open an issue to let us know. Feedback is helpful and motivating to us.

kanna19aero, 2020-06-17:
Thanks Maaphoo. After watching the 10th video I feel a bit confident about
writing a simple program in Arduino. But there is a lot more to go. He is a
great teacher.
Kudos to you on the general tidy up you guys are doing on your
documentations.

Kind regards
Kannan Krishnan

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

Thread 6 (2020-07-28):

Cooling tube problems

Maaphoo, 2020-07-28:
Here are the issues we are facing with the cooling tube:

**Is it even needed? - ** We are extruding from flake and the viscosity is quite low once we have melted the PET. The cooling tube helps us to increase the viscosity of the melt before it leaves the nozzle.  Could we achieve the same results with a better heating profile or easier strategy?

**Alignment - **Because of the bend, the cooling tube must be oriented properly. Because the extruder body is assembled with threaded couplings, the cooling tube must be bent after it is attached to the rest of the extruder body. A better design for coupling the cooling tube to the barrel could fix this.

**Heaters Problematic - ** The cooling tube is heated with fiberglass insulated nichrome wire. The fiberglass is tightly woven and tends to become brittle and break off. We have had the heaters short out against the cooling tube. We have been wrapping the cooling tube in Kapton tape but it doesn't seem like a great solution. We are thinking of threading the nichrome through a different type of fiberglass insulation to solve the issue. What other types of heaters might we use?

**Threads - **The 3/8 in coarse threads cut most of the way through the tube. We need to switch to fine threads. A new coupling design between the cooling tube and the barrel could eliminate the need to cut threads in the tube on this end.

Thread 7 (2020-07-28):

Gear problems

Maaphoo, 2020-07-28:
**Overheating - ** The gears are 3D printed because gears can be hard to find locally. When the extruder has been running for a while, both the motor and the screw get hot and that heat softens the gears. We have overcome this problem by adding metal plates to the large gear, and by printing the smaller gear in either ABS or PET. A cooling fan would also help. At some point, the amount of extra work done to try to avoid buying a gear becomes absurd. Are we there yet?

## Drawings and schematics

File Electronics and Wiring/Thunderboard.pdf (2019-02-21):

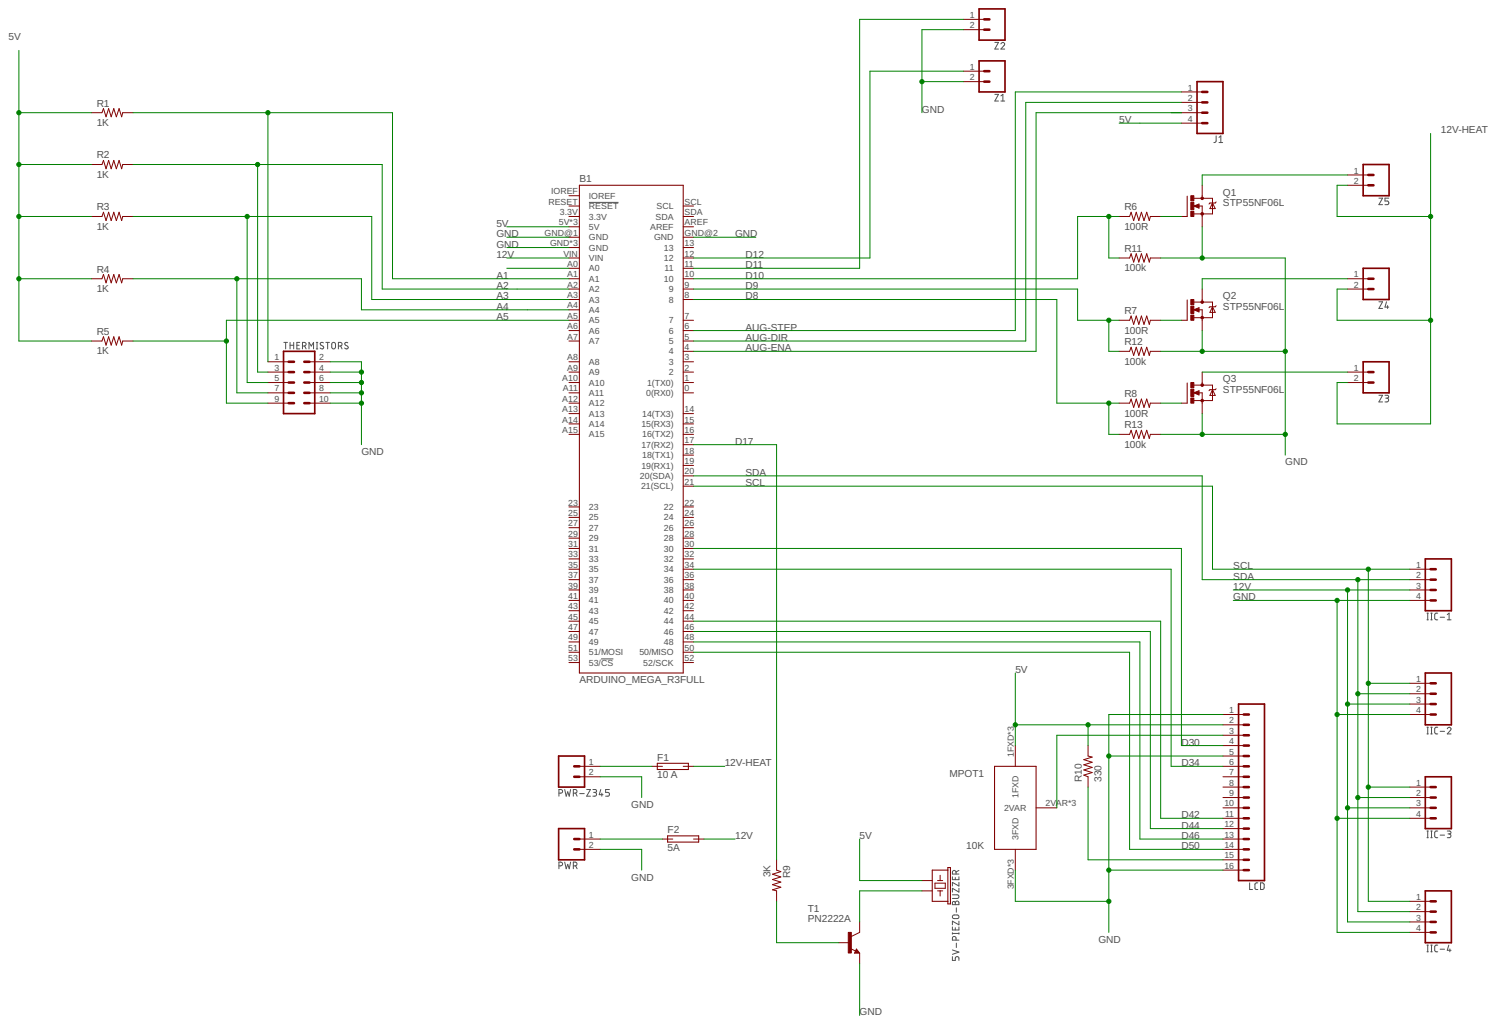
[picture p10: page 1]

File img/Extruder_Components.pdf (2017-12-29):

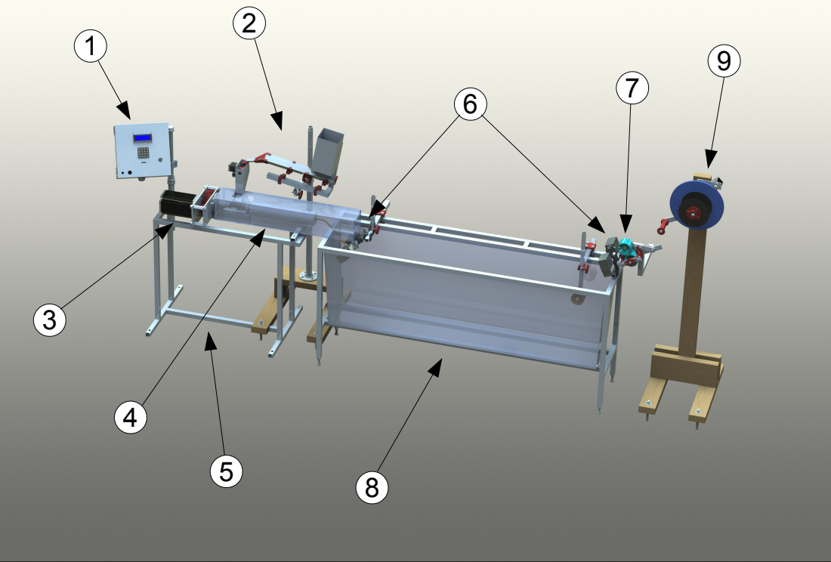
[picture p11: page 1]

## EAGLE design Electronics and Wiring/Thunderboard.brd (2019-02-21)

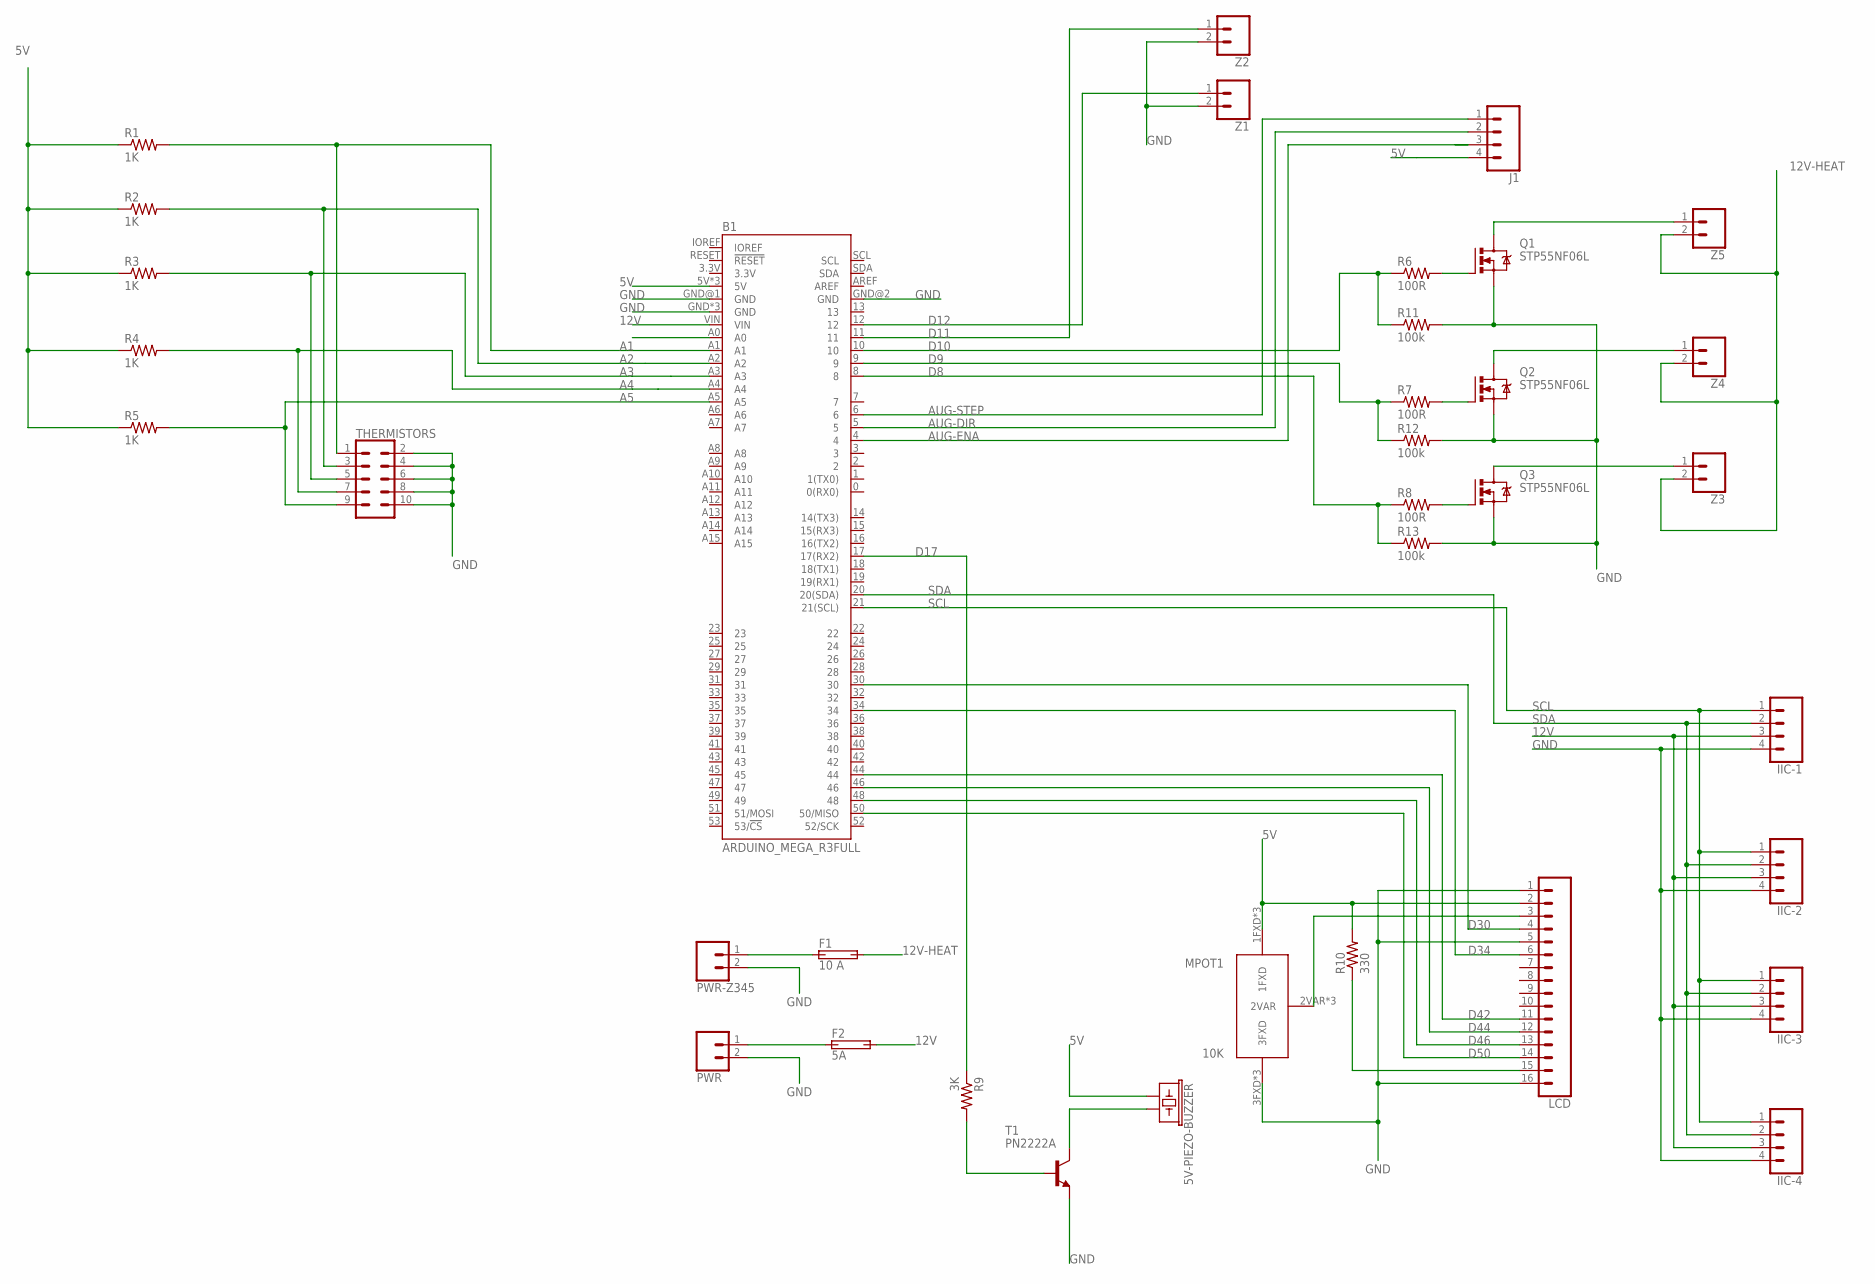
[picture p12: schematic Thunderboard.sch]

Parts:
5V-PIEZO-BUZZER: BUZZER-PTH; BUZZER-12MM
B1: ARDUINO_MEGA_R3FULL; ARDUINO_MEGA_NO_SILK
F1: 10 A; MINI-BLADE
F2: 5A; MINI-BLADE
IIC-1, IIC-2, IIC-3, IIC-4: CONN_04; 1X04
J1: CONN_04; 1X04
LCD: CONN_16; 1X16
MPOT1: 10K; POT-MULTI-PACKAGE
PWR: CONN_023.5MM; SCREWTERMINAL-3.5MM-2
PWR-Z345: CONN_023.5MM; SCREWTERMINAL-3.5MM-2
Q1, Q2, Q3: STP55NF06L; TO-220
R1, R2, R3, R4, R5: 1K; 0207/7
R6, R7, R8: 100R; 0207/7
R9: 3K; 0207/7
R10: 330; 0207/7
R11, R12, R13: 100k; 0207/7
T1: PN2222A; TO92-EBC
THERMISTORS: CONN_05X2NO_SILK; 2X5_NOSILK
Z1, Z2: CONN_02; 1X02
Z3, Z4, Z5: CONN_023.5MM; SCREWTERMINAL-3.5MM-2

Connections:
5V: 5V-PIEZO-BUZZER.+ (1), B1.5V, B1.5V@1 (5V), B1.5V@2 (5V), J1.4, LCD.2, MPOT1.1FXD, MPOT1.P$7 (1FXD), MPOT1.P$8 (1FXD), R1.1, R2.1, R3.1, R4.1, R5.1, R10.2
12V: B1.VIN, F2.2A (2), F2.2B (2), IIC-1.3, IIC-2.3, IIC-3.3, IIC-4.3
12V-HEAT: F1.2A (2), F1.2B (2), Z3.2, Z4.2, Z5.2
A1: B1.A1, R1.2, THERMISTORS.1
A2: B1.A2, R2.2, THERMISTORS.3
A3: B1.A3, R3.2, THERMISTORS.5
A4: B1.A4, R4.2, THERMISTORS.7
A5: B1.A5, R5.2, THERMISTORS.9
AUG-DIR: B1.5, J1.2
AUG-ENA: B1.4, J1.3
AUG-STEP: B1.6, J1.1
D8: B1.8, R8.1, R13.1
D9: B1.9, R7.1, R12.1
D10: B1.10, R6.1, R11.1
D11: B1.11, Z2.1
D12: B1.12, Z1.1
D17: B1.17 (17(RX2)), R9.1
D30: B1.30, LCD.4
D34: B1.34, LCD.6
D42: B1.44, LCD.11
D44: B1.46, LCD.12
D46: B1.48, LCD.13
D50: B1.50 (50/MISO), LCD.14
GND: B1.GND, B1.GND@1 (GND), B1.GND@2 (GND), B1.GND@3 (GND), B1.GND@4 (GND), IIC-1.4, IIC-2.4, IIC-3.4, IIC-4.4, LCD.1, LCD.5, LCD.16, MPOT1.3FXD, MPOT1.P$4 (3FXD), MPOT1.P$5 (3FXD), PWR.2, PWR-Z345.2, Q1.S, Q2.S, Q3.S, R11.2, R12.2, R13.2, T1.E, THERMISTORS.2, THERMISTORS.4, THERMISTORS.6, THERMISTORS.8, THERMISTORS.10, Z1.2, Z2.2
unnamed: 5V-PIEZO-BUZZER.- (2), T1.C
unnamed: R9.2, T1.B
unnamed: Q1.G, R6.2
unnamed: Q2.G, R7.2
unnamed: Q3.G, R8.2
unnamed: LCD.3, MPOT1.2VAR, MPOT1.P$1 (2VAR), MPOT1.P$3 (2VAR)
unnamed: Q1.D, Z5.1
unnamed: Q2.D, Z4.1
unnamed: Q3.D, Z3.1
unnamed: F1.1A (1), F1.1B (1), PWR-Z345.1
unnamed: LCD.15, R10.1
unnamed: F2.1A (1), F2.1B (1), PWR.1
SCL: B1.21 (21(SCL)), IIC-1.1, IIC-2.1, IIC-3.1, IIC-4.1
SDA: B1.20 (20(SDA)), IIC-1.2, IIC-2.2, IIC-3.2, IIC-4.2

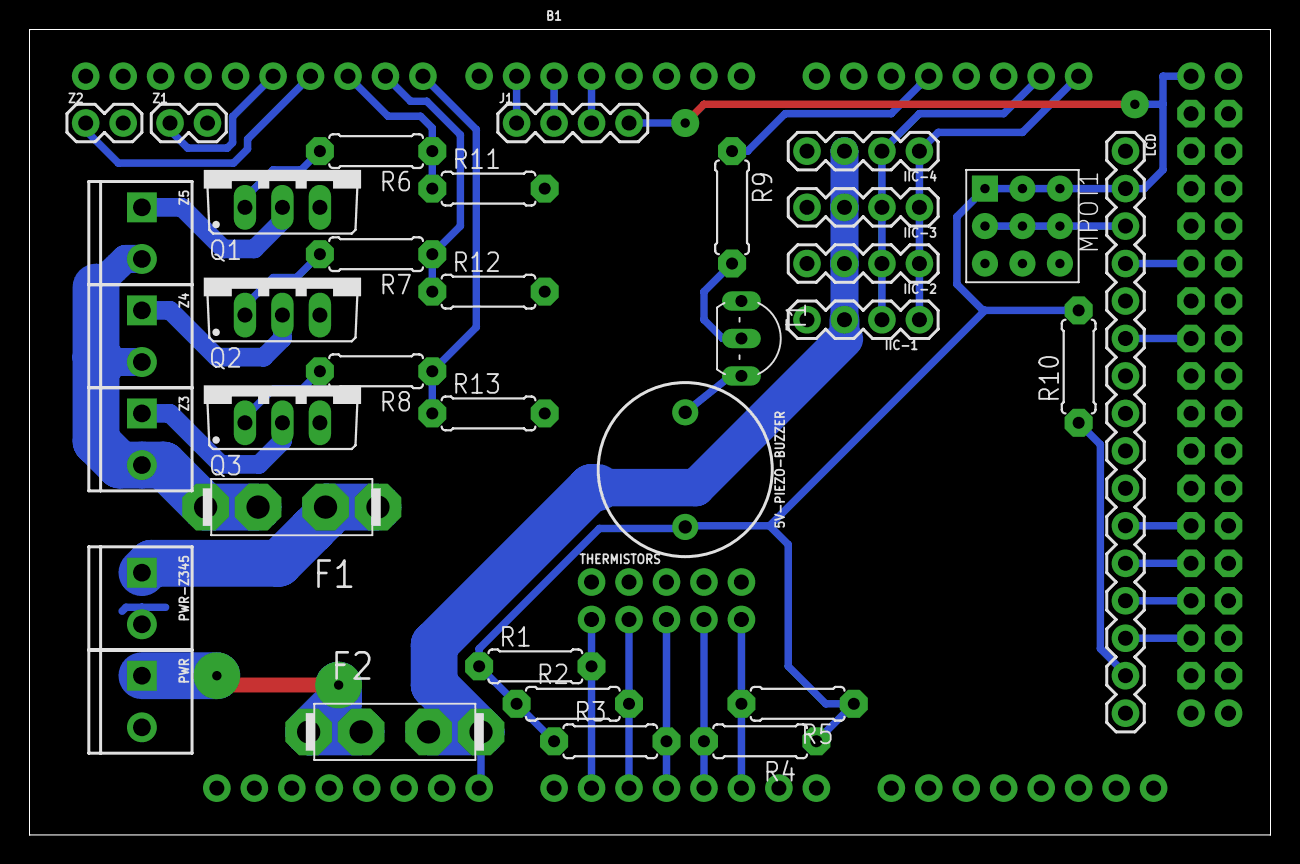
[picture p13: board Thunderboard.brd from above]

Board: 2 copper layers, 84.1 x 54.6 mm, 36 parts (0 on the bottom side), 38 nets.

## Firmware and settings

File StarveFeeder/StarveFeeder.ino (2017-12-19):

#include <Wire.h>
int starveFeederSlaveAddress = 2;
boolean active = false;

//Flags for indicating a change sent by the master arduino
boolean homeFlag;
boolean setGPMFlag;
boolean loadConfigFlag;
boolean fastFill = false;
boolean runForSetTime = false;

enum Mode {
  GRAMS_PER_MIN,
  CYCLES,
};

enum Command {
  ON,
  OFF,
  HOME,
  DUMP_BUCKET,
  FEED_PLASTIC,
  SET_GPM,
  SET_CYCLES,
  LOAD_CONFIG,
  SET_TIME
};

//configuration data that is sent by master arduino
struct Config {
  float gramsPerMin;
  float lumpMass;
  int minFillTime;
  int maxFillTime;
  int startupTime;
  int debounceTime;
  int homePosition;
  int dumpPosition;
  int stepDelay;
  int homingStepDelay;
  int overRotation;
  boolean dir;
  int vibDutyCycle;
  int maxDutyCycle;
  int startupDutyCycle;
} _config;

//General Variables
char key;
int cycles;
Mode mode;

//Time related variables
unsigned long now;//milliseconds
unsigned long dumpTime; //The time at which the plastic is to be dumped from the bucket in milliseconds
unsigned long dumpInterval; //The interval of time between dumps of plastic in milliseconds
unsigned long startTime;
unsigned long startFill;
unsigned long endStartupTime;
unsigned long fillTime;
unsigned long timeToRun;//Used when controller sends a specific amount of time in milliseconds that the starve feeder is to run
unsigned long endRunTime;//Time in milliseconds when the starve feeder is to be shutdown

//Vibrator related Variables
int minDutyCycle = 0;

//Pins
int sensorPin = 2;//The slot sensor pin
int vibPin = 3; //The  vibrator's PWM pin
int enablePin = 4; // the stepper enable pin
int stepPin = 5; //The stepper step pin
int dirPin = 6;//The stepper direction pin

//make state machine
//Setup Finite State Machine
void standby();
void homeBalance();
void prepFillBucket();
void startupVibrator();
void fillBucket();
void beginWait();
void wait();
void dump();
void feed();
void turnOff();

//Names of States
enum states {
  STANDBY,
  HOME_BALANCE,
  PREP_FILL_BUCKET,
  STARTUP_VIBRATOR,
  FILL_BUCKET,
  BEGIN_WAIT,
  WAIT,
  DUMP,
  FEED,
  TURN_OFF
};

states currentState;


//Pointers to State functios
void (*state_table[])() = {
  standby,
  homeBalance,
  prepFillBucket,
  startupVibrator,
  fillBucket,
  beginWait,
  wait,
  dump,
  feed,
  turnOff
};



//Setup
void setup() {
  Serial.begin(115200);
  Wire.begin(starveFeederSlaveAddress);
  Wire.onReceive(receiveEvent);
  Wire.onRequest(requestEvent);
  pinMode(sensorPin, INPUT);
  pinMode(dirPin, OUTPUT);
  pinMode(stepPin, OUTPUT);
  pinMode(enablePin, OUTPUT);
  pinMode(vibPin, OUTPUT);

  digitalWrite(enablePin, HIGH);
  //Set initial state
  _config.homingStepDelay = 2000;
  _config.homePosition = 100;
  _config.dumpPosition = 1600;
  _config.stepDelay = 75;
  _config.gramsPerMin = 4.0;
  _config.lumpMass = 1.0;
  _config.minFillTime = 1000;
  _config.maxFillTime = 10000;
  _config.startupTime = 120;
  _config.debounceTime = 80;
  _config.overRotation = 90;
  _config.vibDutyCycle = 85;
  _config.maxDutyCycle = 160;
  _config.startupDutyCycle = 120;
  _config.dir = 1;

  currentState = STANDBY;
}

void loop() {
  if (Serial.available() > 0) {
    key = (char)Serial.read();
    switch (key) {
      case '1':
        {
          Serial.println("Homing balance");
          digitalWrite(dirPin, !_config.dir);
          currentState = HOME_BALANCE;
        }
        break;
      case '2':
        {
          startTime = millis();
          mode = GRAMS_PER_MIN;
          setGPMFlag = true;
          currentState = PREP_FILL_BUCKET;
        }
        break;
      case '3':
        {
          digitalWrite(enablePin, HIGH);
          analogWrite(vibPin, 0);
          cycles = 0;
          currentState = STANDBY;
        }
        break;
      case '4':
        {
          mode = CYCLES;
          currentState = DUMP;
        }
        break;
      case '5':
        {
          currentState = FEED;
        }
        break;
      case '6':
        {
          cycles = 10;
          mode = CYCLES;
          currentState = PREP_FILL_BUCKET;
        }
        break;
    }
  }

  if (setGPMFlag) {
    dumpInterval = _config.lumpMass / _config.gramsPerMin * 60L * 1000L;
    Serial.println(dumpInterval);
    Serial.print("Mode: ");
    Serial.println(mode);
    setGPMFlag = false;
    dumpTime = millis()+dumpInterval;
  }

  if (loadConfigFlag) {
    dumpInterval = _config.lumpMass / _config.gramsPerMin * 60L * 1000L;
    loadConfigFlag = false;
  }
  
  if (runForSetTime && millis()>=endRunTime){
    turnOff();
  }

  state_table[currentState]();
}

void standby() {
}

void homeBalance() {
  digitalWrite(enablePin, LOW);
  digitalWrite(dirPin, _config.dir);
  for (int i = 0; i < _config.homePosition; i++) {
    PORTD |= B00100000;
    delayMicroseconds(_config.homingStepDelay);
    PORTD &= B11011111;
    delayMicroseconds(_config.homingStepDelay);
  }
  digitalWrite(enablePin, HIGH);
  currentState = STANDBY;
}


void prepFillBucket() {
  //disable stepper
  digitalWrite(enablePin, HIGH);

  //get time and turn jiggler on
  startFill = millis();
  endStartupTime = startFill + _config.startupTime;

  analogWrite(vibPin, _config.startupDutyCycle);
  currentState = STARTUP_VIBRATOR;

}

void startupVibrator() {
  //check to see if bucket is already full
  //Sometimes lots flows out initially
  if (digitalRead(sensorPin)) {

    // record time taken to fill bucket
    fillTime = millis() - startFill;

    //check to see if the bucket was caused by the bucket bouncing
    //if so reset the start time.
    //Is this necessary if the startup time is sufficient?
    if (fillTime < _config.debounceTime) {
      currentState = FILL_BUCKET;
      startFill = millis();
      return;
    }

    //Turn off vibrator
    analogWrite(vibPin, 0);
    //Switch states to BEGIN_WAIT
    currentState = BEGIN_WAIT;
  }

  if (millis() >= endStartupTime) {
    if (fastFill) { // fill bucket without slowing down
      fastFill = false;
      currentState = FILL_BUCKET;
    } else {
      //switch to normal dutycycle now that the vibrator is on
      analogWrite(vibPin, _config.vibDutyCycle);
      currentState = FILL_BUCKET;
    }
  }
}


void fillBucket() {
  //hangout while the bucket is filling.
  //IE - Do nothing
  
  //if we have passed the dumpInterval and it still isn't full
  //Juice it!
  //This will help to keep from getting too far behind
  if (millis() - startFill>dumpInterval){
      analogWrite(vibPin, _config.startupDutyCycle);
  }
  
  //When the sensor pin goes high the bucket is full
  //Capture the time for filling, and switch to BEGIN_WAIT
  if (digitalRead(sensorPin)) {

    // record time taken to fill bucket
    fillTime = millis() - startFill;

    //check to see if the bucket was caused by the bucket bouncing
    //if so reset the start time.
    //Is this necessary if the startup time is sufficient?
    if (fillTime < _config.debounceTime) {
      currentState = FILL_BUCKET;
      startFill = millis();
      return;
    }

    //Turn off vibrator
    analogWrite(vibPin, 0);
    //Switch states to BEGIN_WAIT
    currentState = BEGIN_WAIT;
  }
}

//Remove this state if not needed
void beginWait() {
    if (millis() > dumpTime) {
      fastFill = true;
    }
    currentState = WAIT;
}


void wait() {
  //If the mode is CYCLES switch to the DUMP state automatically
  if (mode == CYCLES) {
    cycles--;
    currentState = DUMP;
    return;
  }

  //wait until the dumpTime and then switch state to dump.
  if (mode == GRAMS_PER_MIN && millis() >= dumpTime) {
    //advance dumpTime
    dumpTime += dumpInterval;


    //Change state
    currentState = DUMP;
  }
}

void dump() {
  //enable Stepper
  digitalWrite(enablePin, LOW);
  //determine next dump time if in automatic mode
  
  //go to dump location
  digitalWrite(dirPin, _config.dir);
  for (int i = 0; i < _config.dumpPosition; i++) {
    PORTD |= B00100000;
    delayMicroseconds(_config.stepDelay);
    PORTD &= B11011111;
    delayMicroseconds(_config.stepDelay);
  }

  //return to home
  digitalWrite(dirPin, !_config.dir);
  for (int i = 0; i < _config.dumpPosition; i++) {
    PORTD |= B00100000;
    delayMicroseconds(_config.stepDelay);
    PORTD &= B11011111;
    delayMicroseconds(_config.stepDelay);
  }
  for (int i = 0; i < _config.overRotation; i++) {
    PORTD |= B00100000;
    delayMicroseconds(_config.stepDelay);
    PORTD &= B11011111;
    delayMicroseconds(_config.stepDelay);
  }
  delay(150);
  digitalWrite(dirPin, _config.dir);
  for (int i = 0; i < _config.overRotation; i++) {
    PORTD |= B00100000;
    delayMicroseconds(_config.stepDelay);
    PORTD &= B11011111;
    delayMicroseconds(_config.stepDelay);
  }
  delay(150);
  digitalWrite(enablePin, HIGH);
  if (mode == CYCLES && cycles == 0) {
    currentState = STANDBY;
  } else {
    //Change state to fill bucket
    currentState = PREP_FILL_BUCKET;
  }
}

void feed() {
  analogWrite(vibPin, _config.startupDutyCycle);
  currentState = STANDBY;
}

void turnOff() {
  analogWrite(vibPin, 0);
  digitalWrite(enablePin, HIGH);
  cycles = 0;
  active = false;
  runForSetTime = false;
  currentState = STANDBY;
}

void turnOn(){
      mode = GRAMS_PER_MIN;
      active = true;
      dumpInterval = _config.lumpMass * 60.0 * 1000.0 / _config.gramsPerMin;
      dumpTime = millis() + dumpInterval;
      currentState = PREP_FILL_BUCKET;
}

void receiveEvent(int bytesRecieved)
{
  byte* bytePtr;
  byte action = Wire.read();


  switch (action) {
    case ON://turn starve feeder on;
      turnOn();
      break;

    case OFF: //turn starve feeder off
      currentState = TURN_OFF;
      break;

    case HOME: //Home the starveFeeder
      currentState = HOME_BALANCE;
      break;

    case DUMP_BUCKET: //Dump
      mode = CYCLES;
      cycles = 0;
      currentState = DUMP;
      break;

    case FEED_PLASTIC: //Feed
      active = true;
      currentState = FEED;
      break;

    case SET_GPM: // set gramsPerMin
      bytePtr = (byte*)&_config.gramsPerMin;
      for (int i = 0; i < 4; i++) {
        *bytePtr = Wire.read();
        bytePtr++;
      }
      setGPMFlag = true;
      break;

    case SET_CYCLES: //set cycles to run
      bytePtr = (byte*)&cycles;
      for (int i = 0; i < 2; i++) {
        *bytePtr = Wire.read();
        bytePtr++;
      }
      active = true;
      mode = CYCLES;
      currentState = PREP_FILL_BUCKET;
      break;

    case LOAD_CONFIG://load the configuration of the starve feeder
      //load the incomming bytes to  _config
      bytePtr = (byte*)&_config;
      while (0 < Wire.available()) {
        *bytePtr = Wire.read();
        bytePtr++;
      }
      loadConfigFlag = true;
      break;
      
    case SET_TIME://Sets an amount of milliseconds for the starve feeder to run. Used for calibration
      bytePtr = (byte*)&timeToRun;
      while (0 < Wire.available()) {
        *bytePtr = Wire.read();
        bytePtr++;
      }
      endRunTime = timeToRun+millis();
      mode = GRAMS_PER_MIN;
      setGPMFlag = true;      
      currentState = PREP_FILL_BUCKET;
      runForSetTime = true;
  }

  //Make sure the buffer is left empty
  while (0 < Wire.available()) {
    *bytePtr = Wire.read();
    bytePtr++;
  }
}

void requestEvent()
{
  Wire.write(active);
}

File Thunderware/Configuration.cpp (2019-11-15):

/*
Configuration.cpp - Library for saving, loading,
and deleting the various configurations both
for the active profile and the physical setup
of the extruder.

Created by Matthew P. Rogge, Februrary 12, 2014.
Released into the public domain.

*/
#include "definitions.h"
#include "Arduino.h"
#include "EEPROMAnything.h"
#include "Configuration.h"

void Configuration::loadDefaultProfile() {

  //General
  profile.profileNumber = -1;
  strcpy(profile.name, "PET 1.85mm");
  profile.diaSetpoint = 3.0;
  profile.density = 1.38;
  profile.tolerance = 0.05;

  //Starve Feeder
  profile.gramsPerMin = 8.0;

  //Auger
  profile.augerRPM = 0.0;

  //Outfeed
  profile.outfeedRPM = 0;



  //Soak Time
  profile.soakTime = 8.0;// minutes for barrel to remain at set point before extruding

  //heat Zones
  profile.zone1InitialSetTemp = 0.0;
  profile.zone2InitialSetTemp = 0.0;
  profile.zone3InitialSetTemp = 0.0;
  profile.zone4InitialSetTemp = 0.0;
  profile.zone5InitialSetTemp = 0.0;
  
  profile.zone1SetTemp = 0.0;
  profile.zone2SetTemp = 0.0;
  profile.zone3SetTemp = 0.0;
  profile.zone4SetTemp = 0.0;
  profile.zone5SetTemp = 0.0;

  //Safety parameters
  profile.minExtrudeTemp = 180; //The minimum temp allowed for extrusion
  profile.maxTemp = 285; //The max temp allowed for any heating zone
  profile.maxPreheatTime = 15; // The max number of minutes allowed for the preheat state.
}


void Configuration::loadDefaultConfig()
{

  //load the physical with the default parameters.
  //EEPROM storage
  physical.loadAutomatically = false;

  //StarveFeeder
  physical.starveFeederSlaveAddress = 2;
  physical.starveFeederLumpMass = 1.00;
  physical.starveFeederHomePosition = 100;
  physical.starveFeederDumpPosition = 1600;
  physical.starveFeederStepDelay = 75;
  physical.starveFeederHomingStepDelay = 2000;
  physical.starveFeederOverRotation = 90;
  physical.starveFeederDirection = 1;
  physical.starveFeederVibDutyCycle = 95;
  physical.starveFeederStartupDutyCycle = 110;
  physical.starveFeederMaxDutyCycle = 160;
  physical.starveFeederMinFillTime = 1000;
  physical.starveFeederMaxFillTime = 10000;
  physical.starveFeederStartupTime = 200;
  physical.starveFeederDebounceTime = 80;


  //auger
  physical.augerPinSet = 0;
  physical.augerStepMode = 8;
  physical.augerDirection = 1;
  physical.augerEnable = 1;
  physical.augerGearRatio = 3.0;

  //Outfeed
  physical.outfeedPinSet = 1;
  physical.outfeedStepMode = 16;
  physical.outfeedDirection = 0;
  physical.outfeedEnable = 0;
  physical.outfeedRollerRadius = 72.13; //
  physical.outfeedMaxRPM = 200.0;
  physical.outfeedMinRPM = 0.0;

  //Spooler
  physical.spoolerPinSet = 2;
  physical.spoolerStepMode = 16;
  physical.spoolerDirection = 0;
  physical.spoolerEnable = 0;
  physical.spoolerDiskRadius = 20.53; //Estimated radius of big wheel roller//Radius of wooden disk relative to motor roller radius
  physical.spoolerCoreRadius = 30.0; //Radius of spool core
  physical.spoolerTraverseLength = 75.00;
  physical.spoolerMotorRollerRadius = 20.34/2;//relative to wooden disk radius

  //Zone 1 heater
#ifdef OLD_PINS
  physical.zone1.heaterPin = 7;
#else  
  physical.zone1.heaterPin = 12;
#endif
  physical.zone1.Kd = 0.0;
  physical.zone1.Ki = 0.15;
  physical.zone1.Kp = 3.4;
  physical.zone1.maxDutyCycle = 100;
  physical.zone1.minDutyCycle = 0;
  physical.zone1.thermistorBCoefficient = 3950;
  physical.zone1.thermistorNumSamples = 20;
  physical.zone1.thermistorPin = 1;
  physical.zone1.thermistorRNom = 100000;
  physical.zone1.thermistorSeriesResistor = 1000;
  physical.zone1.timeBase = 2000;
  physical.zone1.setTemp = 0.0;
  physical.zone1.PWM = false;
  physical.zone1.activeCooling = false;

  //Zone 2 heater
#ifdef OLD_PINS
  physical.zone2.heaterPin = 2;
#else  
  physical.zone2.heaterPin = 11;
#endif
  physical.zone2.Kd = 0.0;
  physical.zone2.Ki = 0.15;
  physical.zone2.Kp = 3.4;
  physical.zone2.maxDutyCycle = 100;
  physical.zone2.minDutyCycle = 0;
  physical.zone2.thermistorBCoefficient = 3950;
  physical.zone2.thermistorNumSamples = 20;
  physical.zone2.thermistorPin = 2;
  physical.zone2.thermistorRNom = 100000;
  physical.zone2.thermistorSeriesResistor = 1000;
  physical.zone2.timeBase = 2000;
  physical.zone2.setTemp = 0.0;
  physical.zone2.PWM = false;
  physical.zone2.activeCooling = false;

  //Zone 3 heater
#ifdef OLD_PINS
  physical.zone3.heaterPin = 3;
#else  
  physical.zone3.heaterPin = 10;
#endif
  physical.zone3.heaterPin = 10;//Was D3
  physical.zone3.Kd = 0.0;
  physical.zone3.Ki = 0.15;
  physical.zone3.Kp = 3.4;
  physical.zone3.maxDutyCycle = 255;
  physical.zone3.minDutyCycle = 0;
  physical.zone3.thermistorBCoefficient = 3950;
  physical.zone3.thermistorNumSamples = 20;
  physical.zone3.thermistorPin = 3;
  physical.zone3.thermistorRNom = 100000;
  physical.zone3.thermistorSeriesResistor = 1000;
  physical.zone3.timeBase = 2000;
  physical.zone3.setTemp = 0.0;
  physical.zone3.PWM = true;
  physical.zone3.activeCooling = false;
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

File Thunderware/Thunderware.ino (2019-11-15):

/*
  Thunder Head Filament Extruder Firmware

  The Thunder Head extruder is a small scale extruder
  that makes 3D printing filament.

  Created by Matthew P. Rogge, Februrary 12, 2014.
  Released into the public domain.

*/
#include "definitions.h"
#include <stdio.h>
#include <string.h>
#include <math.h>
#include <LiquidCrystal.h>
#include <Wire.h>
#include <avr/pgmspace.h>
#include <EEPROM.h>
#include "Keypad.h"
#include "PID_v1.h"
#include "EEPROMAnything.h"
#include "Thermistor.h"
#include "Configuration.h"
#include "Buzzer.h"
#include "Heater.h"
#include "StepperMotor.h"
#include "FastPWM.h"
#include "Spooler.h"
#include "StarveFeeder.h"
#include "Safety.h"
#include "QCDiaSensor.h"
#include "Menu.h"
//#include <MemoryFree.h>


Configuration configuration;
#include "menuData.h"




//Setup Finite State Machine
enum ExtruderStates {
  STANDBY,
  BEGIN_PREHEAT,
  PREHEAT,
  BEGIN_SOAK,
  SOAK,
  BEGIN_LOAD_FILAMENT,
  LOAD_FILAMENT,
  BEGIN_EXTRUDE,
  EXTRUDE
} currentState;

void standby();
void beginPreheat();
void preheat();
void beginSoak();
void soak();
void beginLoadFilament();
void loadFilament();
void beginExtrude();
void extrude();

//Pointers to State functions
void (*state_table[])() = {
  standby,
  beginPreheat,
  preheat,
  beginSoak,
  soak,
  beginLoadFilament,
  loadFilament,
  beginExtrude,
  extrude
};

// lcd pins
#ifdef OLD_PINS
const byte LCD_RS  = 22;
const byte LCD_EN  = 24;
const byte LCD_D4  = 26;
const byte LCD_D5  = 28;
const byte LCD_D6  = 30;
const byte LCD_D7  = 32;

#else //The following pins are used with Thunderboard PCB
const byte LCD_RS  = 30;
const byte LCD_EN  = 34;
const byte LCD_D4  = 44;
const byte LCD_D5  = 46;
const byte LCD_D6  = 48;
const byte LCD_D7  = 50;

#endif

const byte LCD_ROWS = 4;
const byte LCD_COLS = 20;

//initialize library with LCD interface pins
LiquidCrystal lcd(LCD_RS, LCD_EN, LCD_D4, LCD_D5, LCD_D6, LCD_D7);

//Keypad Rows and Columns
const byte ROWS = 4;
const byte COLS = 4;

//Membrane Kpd initialize keypad pins

byte rowPins[COLS] = {23, 25, 27, 29};
byte colPins[ROWS] = {31, 33, 35, 37};

//Keymap
char keys[ROWS][COLS] = {
  {'1', '2', '3', 'A'},
  {'4', '5', '6', 'B'},
  {'7', '8', '9', 'C'},
  {'*', '0', '#', 'D'}
};


Keypad kpd = Keypad( makeKeymap(keys), rowPins, colPins, ROWS, COLS);

char key;//The key that is pressed

//Initialize objects
Buzzer buzzer;

StarveFeeder starveFeeder(&configuration);

Heater zone1(&configuration.physical.zone1);
Heater zone2(&configuration.physical.zone2);
Heater zone3(&configuration.physical.zone3);
Heater zone4(&configuration.physical.zone4);
Heater zone5(&configuration.physical.zone5);

StepperMotor auger(&configuration, configuration.physical.augerPinSet);

//Outfeed outfeed(&configuration.physical.diaSensorRegMap);
Outfeed outfeed(&configuration);

QCDiaSensor qcDiameterSensor(&configuration.physical.qcDiaSensorRegMap);

//Spooler spooler(&configuration);

Safety safety(&configuration);

Menu mainMenu(mainItems, sizeof(mainItems) / sizeof(mainItems[0]), &lcd, &kpd);
Menu preheatMenu(preheatItems, sizeof(preheatItems) / sizeof(preheatItems[0]), &lcd, &kpd);
Menu soakMenu(soakItems, sizeof(soakItems) / sizeof(soakItems[0]), &lcd, &kpd);
Menu loadFilamentMenu(loadFilamentItems, sizeof(loadFilamentItems) / sizeof(loadFilamentItems[0]), &lcd, &kpd);
Menu extrudeMenu(extrudeItems, sizeof(extrudeItems) / sizeof(extrudeItems[0]), &lcd, &kpd);
Menu* activeMenu;


//Include state functions
#include "Extrude.h"
#include "Preheat.h"
#include "Safety.h"
#include "TestReporting.h"

void setup()
{

  Serial.begin(250000);
  while (!Serial); // while the serial stream is not open, do nothing:
  Wire.begin();
  lcd.begin(20, 4); //Start up LCD
  lcd.clear();
  activeMenu = &mainMenu;
  currentState = STANDBY;

  auger.disable(); // Why is this necessary. If not here, there is high frequency signal on the auger step pin.

  configuration.loadConfig();
  activeMenu->reset();
  //  spooler.disable();
  outfeed.disable();

  buzzer.setMsg(Buzzer::POWER_ON);
}

// Timing variables used for data display
static unsigned long refreshDisplayTime;
static unsigned long reportDiaTime;
static unsigned int reportDiaInterval = 200;

void loop() {
  static unsigned long now;

  //Allow for keyboard input
  key = kpd.getKey();
  if (Serial.available() > 0) {
    key = (char)Serial.read();
  }

  if (key) {
    //Serial.print("freeMemory()=");
    //Serial.println(freeMemory());
    Serial.println(key);
  }

  switch (key) {
    case 'A':
    case 'q':
      activeMenu->up();
      break;
    case 'B':
    case 'w':
      activeMenu->down();
      break;
    case 'C':
    case 'e':
      activeMenu->select();
      break;
    case 'D':
    case 'r':
      activeMenu->back();
      break;

    case '1':
      activeMenu->increase();
      break;

    case '4':
      activeMenu->decrease();
      break;

    case '*'://reset LCD. Use when lcd goes crazy
      lcd.begin(20, 4);
      activeMenu->display();
      break;
  }

  state_table[currentState]();

  ////Activate the heaters for testing
  zone1.activate();
  zone2.activate();
  zone3.activate();
  zone4.activate();
  zone5.activate();

  now = millis();
  if (currentState == EXTRUDE) {
    if (now >= reportDiaTime) {
      //Get Diameters from Diameter sensors
      outfeed.readDiaAndRPM();
      qcDiameterSensor.readDia();

      //Print data to serial so that Processing can graph it.
      //      Serial.print((now - extrudeStartTime) / 1000);
      //      Serial.print("\t");
      //      Serial.print(outfeed.getDia(), 4);
      //      Serial.print("\t");
      //      Serial.print(qcDiameterSensor.getDia(), 4);
      //      Serial.print("\t");
      //      Serial.println(outfeed.getRPM(), 2);

      //Advance the time
      reportDiaTime = millis() + reportDiaInterval;
    }
  }

  if (now >= refreshDisplayTime) {
    //update display variables
    //Temps
    zone1Temp = zone1.getTemp();
    zone2Temp = zone2.getTemp();
    zone3Temp = zone3.getTemp();
    zone4Temp = zone4.getTemp();
    zone5Temp = zone5.getTemp();

    //Diameter
    outfeed.readDiaAndRPM();
    qcDiameterSensor.readDia();
    //soakTime remaining
    if (currentState == SOAK) {
      makeTimeString(soakTimeRemaining, soakEndTime - millis());
    }


    //load filament Time
    if (currentState == LOAD_FILAMENT) {
      makeTimeString(loadFilamentTimeRemaining, loadFilamentEndTime - millis());
    }
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

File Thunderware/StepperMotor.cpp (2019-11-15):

/*
  StepperMotor.cpp - Library for controlling the 3 stepper motors
  in the extruder. The motors are driven using a fast PWM signal
  (Timer1, Timer2 and Timer4). PWM is used because angular velocity
  is more important than angular position the PWM signal works well
  and frees up the processor for other jobs.

  Created by Matthew P. Rogge, Februrary 12, 2014.
  Released into the public domain.
*/

#include "definitions.h"
#include "Arduino.h"
#include "StepperMotor.h"
//#include "config.h"
#include "Configuration.h"

class Configuration;

StepperMotor::StepperMotor(Configuration* configuration, int pinSet) : _timer(pinSet)
{
  _pinSet = pinSet;
  _configuration = configuration;
  //Set Direction, Step and Enable pins to output
  switch (_pinSet){
    case 0://SET_8_14_6
      _ratio = (float)_configuration->physical.augerStepMode*(float)_configuration->physical.augerGearRatio;
      
#ifdef OLD_PINS      
      DDRJ |= B00000010; //Direction, Pin 14 to output
#else
      pinMode(5, OUTPUT);//Direction pin
#endif

      DDRH |= B00001000; // Step pin 6 to output
      DDRH |= B00100000;//Enable pin 8 to output

      //set Auger Stepper direction (pin 14)
      if (_configuration->physical.augerDirection){
#ifdef OLD_PINS
        PORTJ |= B00000010;// Direction is forward so set the pin HIGH
#else
        digitalWrite(5, HIGH);
#endif
      }else{
#ifdef OLD_PINS
        PORTJ &= B11111101; // Direction is Backward so set the pin LOW
#else
        digitalWrite(5, LOW);
#endif
      }

      break;

    case 1://SET_11_15_12
      _ratio = configuration->physical.outfeedStepMode;

      DDRJ |= B00000001; //Direction, pin 15 to output
      DDRB |= B01000000; //Enable, pin 12 to output
      DDRB |= B00100000; //Step, pin 11 to output

      //set outfeed Stepper direction (pin 15)
      if (configuration->physical.outfeedDirection){
        PORTJ |= B00000001;// Direction is forward so set the pin HIGH
      }else{
        PORTJ &= B11111110; // Direction is backward so set the pin LOW
      }

      break;

    case 2://SET_10_16_9
        _ratio = configuration->physical.spoolerStepMode;

      DDRH |= B00000010; //Direction, pin 16 to output
      DDRH |= B01000000; //Enable, pin 9 to output
      DDRB |= B00010000;//Step, pin 10 to output

      //set spool Stepper direction pin (pin 16)
      if (configuration->physical.spoolerDirection){
        PORTH = PORTH | B00000010;// Direction is backward so set the pin HIGH
      }else{
        PORTH = PORTH & B11111101; // Direction is forward so set the pin LOW
      }

      break;

    case 3://SET_46_48_5
//      _ratio = configuration->physical.starveFeederStepMode;
//
//      DDRL |= B00001000; //Direction, pin 46 to output
//      DDRL |= B00000010; //Enable, pin 48 to output
//      DDRE |= B00001000;//Step, pin 5 to output

      //set Starve Feeder Stepper direction pin (pin 46)
//      if (configuration->physical.starveFeederDirection){
//        PORTL = PORTL | B00001000;// Direction is backward so set the pin HIGH
//      }else{
//        PORTL = PORTL & B11110111; // Direction is forward so set the pin LOW
//      }
      break;
    }
    disable(); // Make sure that the steppers begin disabled
 }

float StepperMotor::getFrequency(){

	return _timer.getFrequency();
}

void StepperMotor::setRPM(double RPM){
  _rpm = RPM;
  float freq = RPM/60.0*200.0*(float)_ratio;
 _timer.setFrequency(freq);
}

float StepperMotor::getRPM(){return _rpm;}


 //The following should be done before Setting the Spool RPM

   //Make sure the spoolRPM is updated
//   calcSpoolRPM();

void StepperMotor::enable() {

  switch (_pinSet){
    case 0://SET_6_7_8
      //Auger Stepper pin 8
      //disable is backwards for the KL stepper driver being used. Set LOW
      if (_configuration->physical.augerEnable){
      PORTH |= B00100000;
      }else{
      PORTH &= B11011111;
      }
      break;

    case 1://SET_11_15_12
      //Outfeed Stepper pin 12
      //disable outfeed stepper by setting the enable pin HIGH
      if (_configuration->physical.outfeedEnable){
      PORTB |= B01000000;
      }else{
      PORTB &= B10111111;
      }
      break;

    case 2://SET_10_16_9
       //Spool Stepper pin 9
       //disable Spool stepper by setting the enable pin HIGH
      if (_configuration->physical.spoolerEnable){
//          digitalWrite(9, HIGH);
        PORTH |= B01000000;
      }else{
//          digitalWrite(9, LOW);
        PORTH &= B10111111;
      }
      break;

    case 3://SET_46_48_5
       //StarveFeeder Stepper pin 48
       //enable StarveFeeder stepper by setting the enable pin HIGH
//      if (_configuration->physical.starveFeederEnable){
//       PORTL |= B00000010;
//      }else{
//       PORTL &= B11111101;
//      }
       break;
     }
}

void StepperMotor::disable() {
  switch (_pinSet){
    case 0://SET_6_7_8
      //Auger Stepper pin 3
      if (!_configuration->physical.augerEnable){
        PORTH |= B00100000;
      }else{
        PORTH &= B11011111;
      }

      break;

    case 1://SET_11_15_12
      //Outfeed Stepper pin 12
      //disable outfeed stepper by setting the enable pin Low
      if (!_configuration->physical.outfeedEnable){
      PORTB |= B01000000;
      }else{
      PORTB &= B10111111;
      }
      break;

    case 2://SET_10_16_9
       //Spool Stepper pin 9
       //disable Spool stepper by setting the enable pin low
      if (!_configuration->physical.spoolerEnable){
         PORTH |= B01000000;
      }else{
       PORTH &= B10111111;
      }
      break;

    case 3://SET_46_48_5
       //StarveFeeder Stepper pin 48
       //disable StarveFeeder stepper by setting the enable pin low
//      if (!_configuration->physical.starveFeederEnable){
//       PORTL |= B00000010;
//      }else{
//       PORTL &= B11111101;
//      }

      break;
  }
  setRPM(0.0);// turn the PWM to the pin off for safety
}
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

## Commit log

2016-09-03 Initial Bulk Commit :heart:
    [!keypad.SLDASM, 1 in Floor Flange.SLDPRT, 1 to 1_2 in pipe reducer.SLDPRT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]
2016-09-03 Added stepper
2016-09-04 Revised heating information
2016-09-04 Added thermistors
2016-09-04 Added filament picture
2016-09-04 Added flow images
2017-12-15 Removed old CAD files and began playing with READEME.md
    [!keypad.SLDASM, 1 in Floor Flange.SLDPRT, 1 to 1_2 in pipe reducer.SLDPRT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]
2017-12-19 Added more to the README file and also added code files.
    [Configuration.h, menuSpreadSheet.xlsx]
2017-12-19 Deleted assembly and images
2017-12-28 Added ReadMe section about the parts of the extruder.
2017-12-28 Added the Extruder_Components.jpg image and bolded a few items in the README file
2017-12-29 Modified extruder components diagram and text. Switched to Open Office.
2017-12-29 Added section on operating the extruder.
2018-02-05 Added images of Auger Motor and Gear Box parts.
2018-02-25 Adding images for Extruder body and some tools
2018-02-28 Update README.md
    adding donate button
2018-02-28 Update README.md
    Fixing donate button
2018-07-16 Adding images for the Auger gear and motor.
2018-07-18 Updating images of the Auger gear box and motor.
2018-07-18 Updating image of auger gear box and motor
2018-07-19 updating extruder body images
2018-07-19 adding video frame
2018-07-19 Updating images in extruder body
2018-07-19 Updating extruder body.
2018-07-30 Adding images for extruder stand wiki.
2018-07-31 Correcting the water bath weldment drawings.
2018-08-18 Updating images for Vibratory Conveyor
2018-08-18 Adding video frame for vibratory conveyor stand.
2018-08-18 Adding images for Vibratory Conveyor.
2018-08-18 Adding video frame and main image for Vibratory Conveyor.
2018-08-27 updating images for primary diameter sensor
2018-08-27 adding video images for primary diameter sensor
2018-08-27 Adding images for QC diameter sensor
2019-01-30 Adding the Thunderboard schematic and the general wiring schematic. Also adding some images used in the documentation.
    [Thunderboard.brd, Thunderboard.sch, Wiring.sch]
2019-01-30 Updating the wiring schematic.
    [Thunderboard.brd, Wiring.sch]
2019-01-31 Adding Wiring diagram image
2019-01-31 Adding PCB image
2019-02-01 Updating electronics files
    [Thunderboard.brd, Thunderboard.sch, Wiring.sch]
2019-02-21 Changes made after testing the Thunderboard. Switched from Tip120 to a power fet STP55NF06L.
    [Thunderboard.brd, Thunderboard.sch]
2019-02-21 Setting default extrusion profile to all zeros. That will prevent the bad situation where the auger stepper begins turning and the barrel is still cold. Note that Preheat and Soak states are skipped 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
    [Configuration.cpp]
2019-11-15 Uploading more current image of machine.
2019-11-15 Updating code so that the code in the master branch can handle both old and new versions of electionics using #define/#ifdef calls.
    [Configuration.h]
2019-11-15 Fixed a bug with the outfeed. Compiles but not tested.
    [Outfeed.cpp]
2019-12-15 Uploading images for high voltage electronics
2019-12-15 Adding images and files for low voltage electronics

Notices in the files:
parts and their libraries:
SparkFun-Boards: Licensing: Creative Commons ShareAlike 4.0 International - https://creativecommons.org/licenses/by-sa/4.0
